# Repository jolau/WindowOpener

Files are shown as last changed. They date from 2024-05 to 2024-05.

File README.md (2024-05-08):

# WindowOpener
Living in a place without central ventilation, I still wanted to have automatically regulated room climate. Using 3D printing, I designed a system that could automatically open and close the window. Initially intended for my bedroom, the design proved too noisy. I repurposed the system for the bathroom, where it could automatically regulate the humidity. The window opener would open the bathroom window when taking a shower and close it again once the humid air was out. Such a system is not only convenient, but also saves energy by only opening the window as long as necessary.

Video: https://www.youtube.com/watch?v=BI4nM2m5Y50

## Hardware Design

While many commercial window opener systems use expensive linear actuators, I looked for a more cost-effective DIY solution. I opted for a continuous rotation RC servo motor for actuation, mounted on the window casement. This motor drives a large spur gear fixed to the window frame, with two end switches ensuring the motor stops when the window is fully opened or closed. Of course, the window can still be opened and closed manually.
I discovered the design limitation of this approach: the center of rotation of the stationary spur gear must align perfectly with the window hinge. While this approach works with my custom solution, such a requirement would not be feasible for commercial products.

## Software & Automation

The window opener is controlled by the popular ESP8266 microcontroller with built-in Wi-Fi. I programmed it using the ESPHome framework, which easily integrates with our Home Assistant home automation system. Additionally, I installed a Zigbee humidity sensor in the bathroom. I used pyscript on Home Assistant to automate the system, opening the window if the bathroom’s humidity exceeds the apartment’s average by a certain threshold and closing it once the humidity drops below a predefined level. For quick ventilation after using the toilet, one can press the IKEA TRADFRI Zigbee remote to open the window for 15 minutes. A long button press can also turn off the automatic opening, which is handy when taking a long bath.

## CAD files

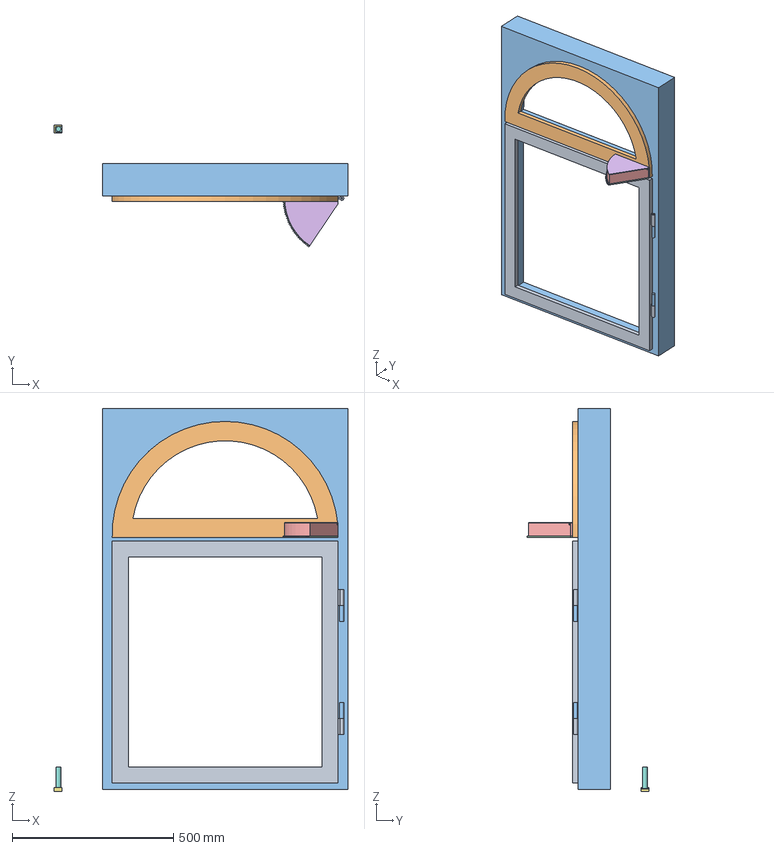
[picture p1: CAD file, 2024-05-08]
model/WindowOpener [Bathroom]_v17.step
910.0 x 377.9 x 1186.0 mm
Casement
Frame
Spur Gear (180 teeth)
SpurGearMount
FixedGearLid
Base
Bar

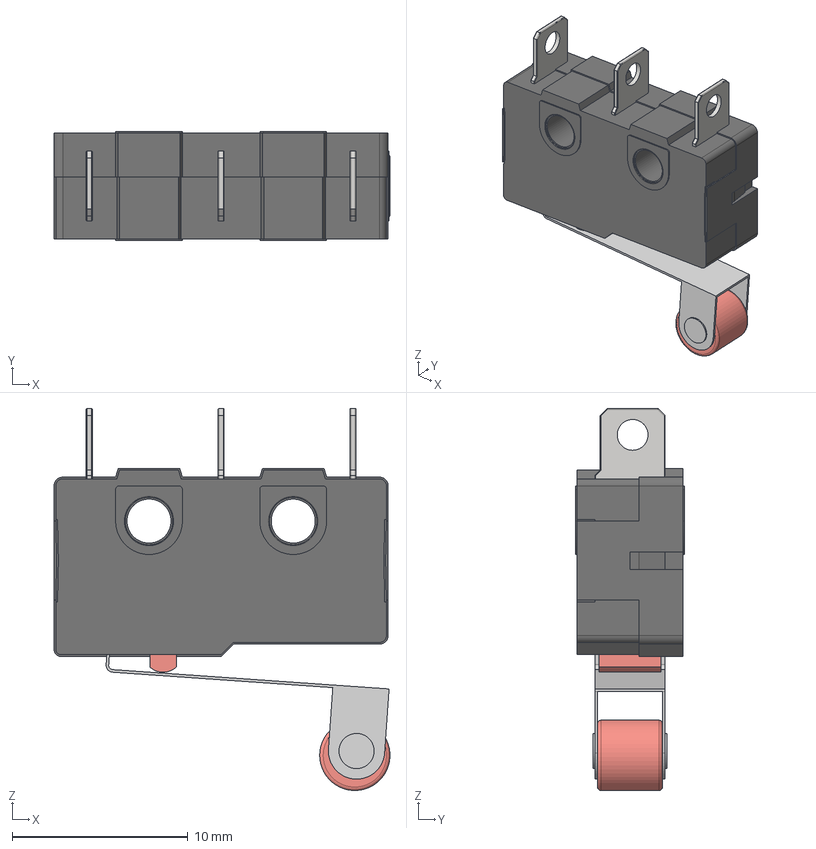
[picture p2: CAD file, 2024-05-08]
model/end_switch_v1.step
19.1 x 6.20 x 21.7 mm
Button
Lever
Wheel

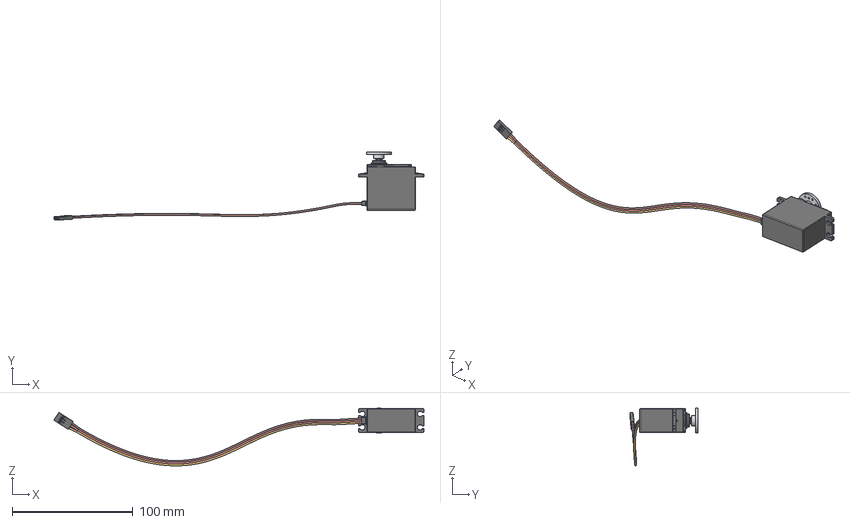
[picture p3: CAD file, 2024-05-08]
model/Servo30kg_v5.step
307.0 x 56.5 x 48.0 mm
Golden part
Wires
Metal bits
RoundHorn

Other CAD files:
model/Servo30kg_v5.3mf
model/Servo30kg_v5.f3d
model/WindowOpener [Bathroom]_v17.3mf
model/end_switch_v1.3mf
model/end_switch_v1.f3d

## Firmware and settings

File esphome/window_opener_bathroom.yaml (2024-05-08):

esphome:
  name: window_opener_bathroom
  platform: ESP8266
  board: d1_mini

wifi:
  ssid: "EngineeringResidency"
  password: "Letmeinnow"
  fast_connect: true
  # Enable fallback hotspot (captive portal) in case wifi connection fails
  ap:
    ssid: "Window Opener Bathroom"
    password: "OgbdD0g36O0e"

captive_portal:

# Enable logging
logger:

# Enable Home Assistant API
api:
  password: "Wlcm2thftr"

ota:
  password: "Wlcm2thftr"

status_led:
  pin: D4

binary_sensor:
  - platform: gpio
    id: close_endstop_binary_sensor
    name: "Bathroom Window Closed"
    pin: 
      number: D7
      mode: INPUT
      inverted: true
    on_press:
      then:
      - cover.control:
          id: window_opener
          position: 0%
  - platform: gpio
    id: open_endstop_binary_sensor
    name: "Bathroom Window Open"
    pin:
      number: D3
      mode: INPUT_PULLUP
      inverted: true
    on_press:
      then:
      - cover.control:
          id: window_opener
          position: 100%

output:
  - platform: esp8266_pwm
    id: pwm_output
    pin: D1
    frequency: 50 Hz

servo:
  - id: window_servo
    output: pwm_output
    min_level: 5%
    idle_level: 7.5%
    max_level: 10%

cover:
  - platform: endstop
    name: "Bathroom Window Opener"
    id: window_opener
    device_class: window
    max_duration: 8s

    open_action:
      - servo.write:
          id: window_servo
          level: 25%
    open_duration: 5s
    open_endstop: open_endstop_binary_sensor

    close_action:
      - servo.write:
          id: window_servo
          level: -25%
    close_duration: 4s
    close_endstop: close_endstop_binary_sensor

    stop_action:
      - servo.write:
          id: window_servo
          level: 0%
